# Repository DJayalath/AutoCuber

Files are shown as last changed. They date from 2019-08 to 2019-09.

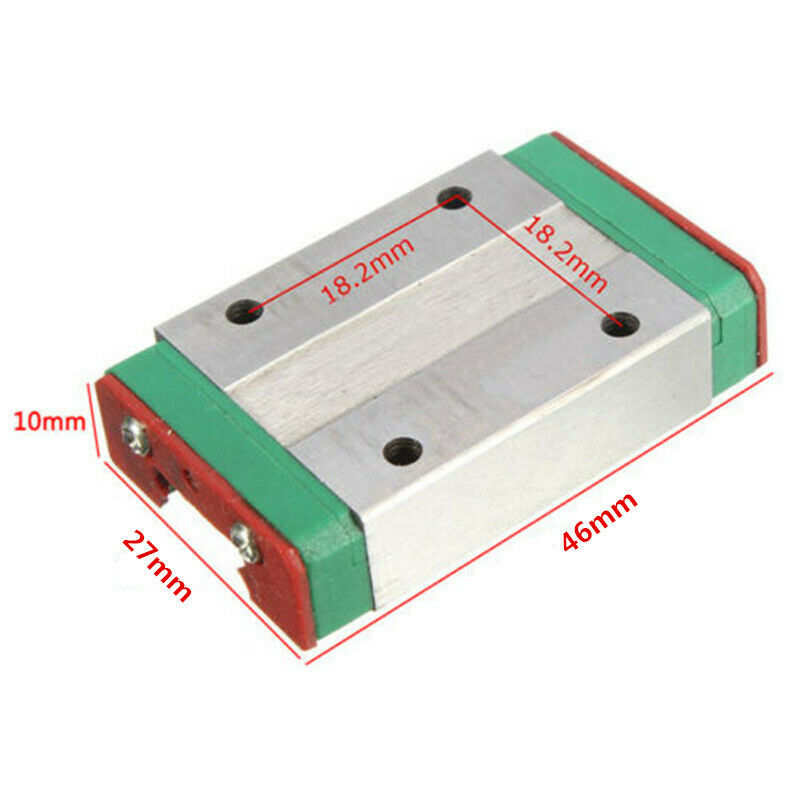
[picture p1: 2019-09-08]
Designs/MGN12H_Block_Measurements.jpg

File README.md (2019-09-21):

# AutoCuber
A fully automated Rubik's cube solving machine

### Video demonstration
Stage 1: Scan all 6 faces of the cube to retrieve cube state

Stage 2: Calculate solution and solve

https://www.youtube.com/watch?v=FX_zLw3P7Gw

(Video recorded prior to optimization updates - current version wastes no rail movements)

### Organisation
- `Designs` contains 3D models created for this project (as well as the custom PCB design)
- `RPI` contains the python programs written to scan in a cube's state and calculate a solution (used on RPI3B w/ Cam)
- The root directory contains the C++ program to control the stepper motors and interpret serial communication (Arduino Mega)

### How does it work?
#### Cube interaction
The machine is similar to others you may have seen before. 4 stepper motors on linear rails are able to turn faces of the cube
in the horizontal plane. 4 more stepper motors attached using a rod can pull and push the other stepper motors along their rails.
Through this system, it is possible to turn any face of the cube, either directly or after rotating the cube. All the motors are 
controlled by DRV8825 stepper motor drivers, connected to an Arduino Mega. The stepper motor drivers are soldered to two identical custom PCBs.
#### Finding the cube's state
A Raspberry Pi 3B is used with a camera to take an image of each face of the cube (Commands are sent to the Arduino Mega to rotate
the cube such that the face needed is facing the camera). The picture is cropped and rotated by a fixed constant amount to contain
only the face of the cube. It is then split into 9 equal segments to isolate individual tiles. k-means clustering is used to find
the dominant colour in each tile. This RGB value is converted to HSL such that linear comparisons can be made between colours. The 
shortest euclidian distance is used to determine which class the colour belongs to. The entire cube is then mapped using this technique.
#### Solving the cube
The `ckociemba` library is used to find a solution using Kociemba's method. The set of instructions to solve the cube are sent 
one by one to the Arduino Mega which uses the motors to complete each move on the cube. **TODO: A custom implementation of 
Kociemba's algorithm.**
### Other Pictures




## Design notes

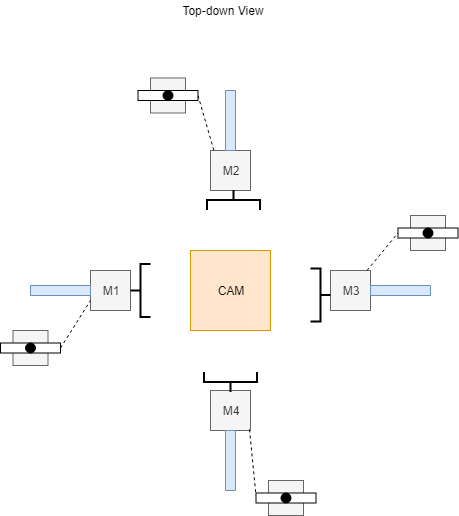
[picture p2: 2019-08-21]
Designs/TopDown.png

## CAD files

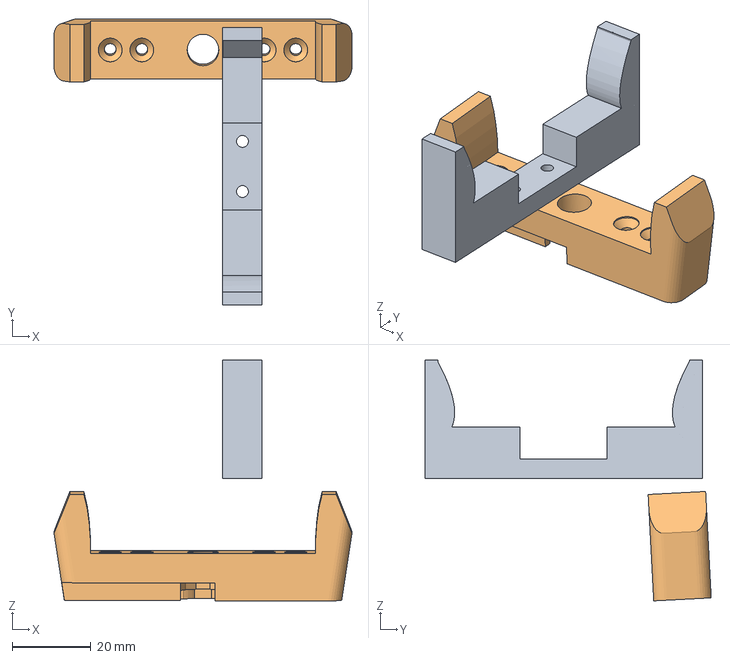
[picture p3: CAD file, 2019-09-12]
Designs/Gripper/Gripper.FCStd
75.5 x 72.6 x 61.0 mm
rcr_gripper

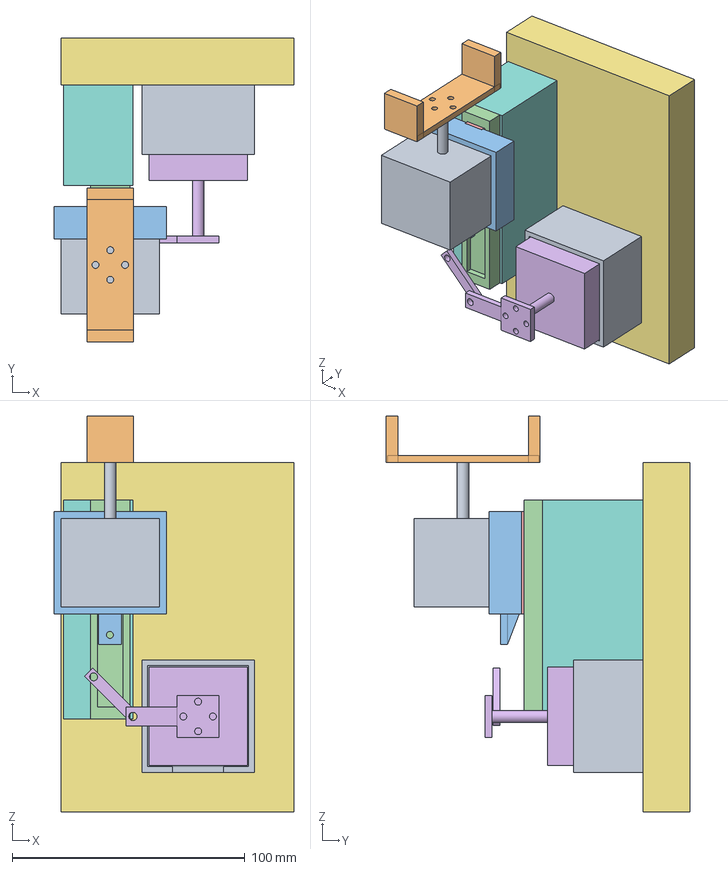
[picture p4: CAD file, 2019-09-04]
Designs/LayoutDesign.FCStd
103.0 x 130.3 x 170.0 mm
17HS4401
Gripper
SildeFullTray
SlidingModule
SlideSection001
SlidingMotorConfig
MechBase
SliderBase
LinearTray

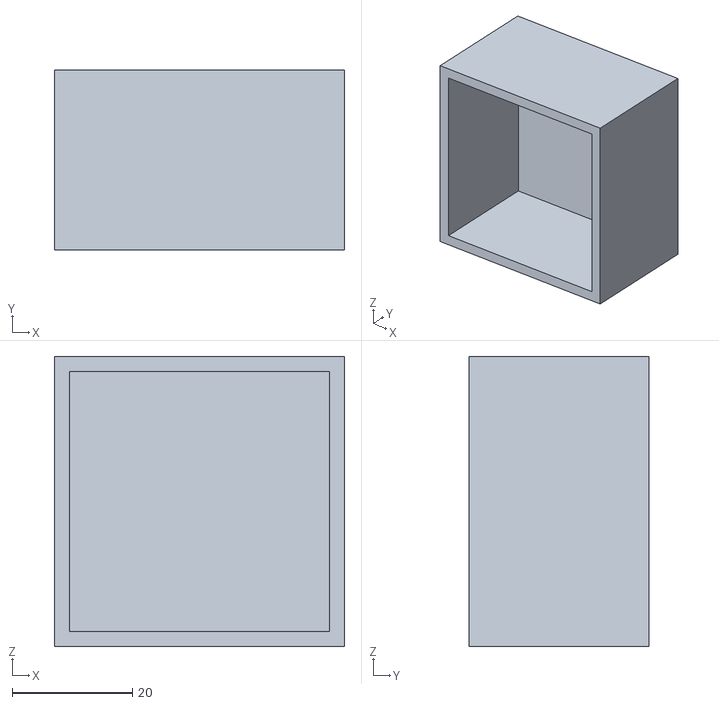
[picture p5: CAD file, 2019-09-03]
Designs/LayoutDesign/LinearMotorTray.stl
48.3 x 30.0 x 48.3

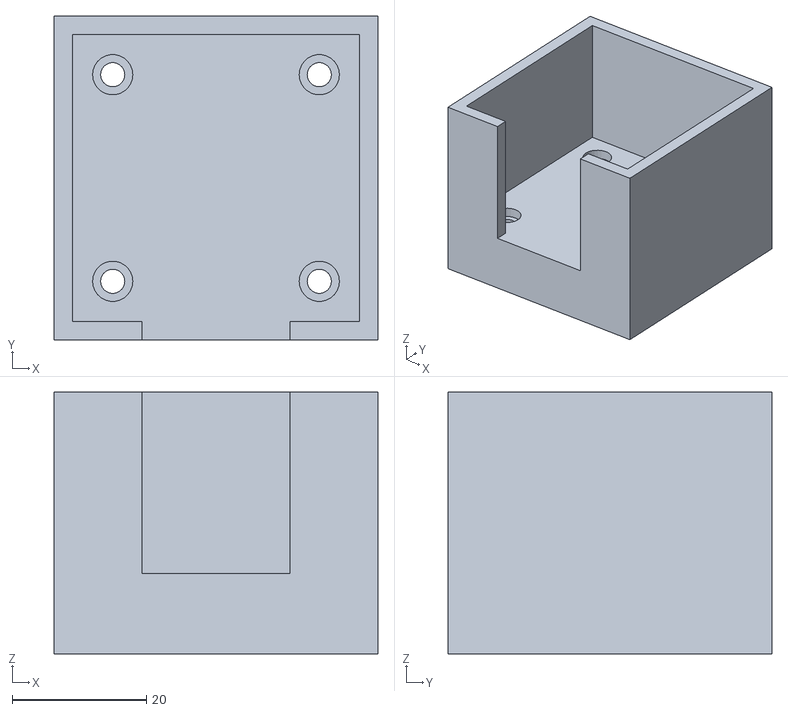
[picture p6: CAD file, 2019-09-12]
Designs/LinearRail/LinearTrayV-1-1.stl
48.3 x 48.3 x 39.0

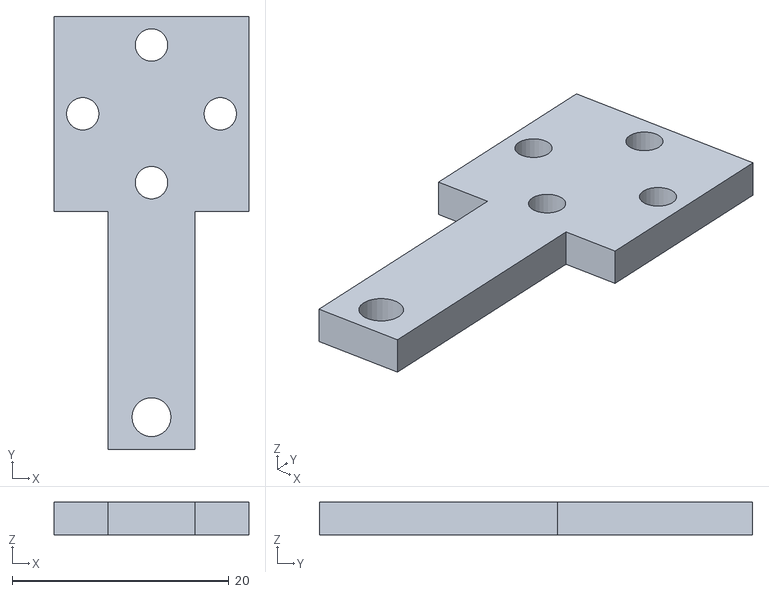
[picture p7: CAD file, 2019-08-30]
Designs/Slider/SlideMotorArmExtension.stl
18.0 x 40.0 x 3.00

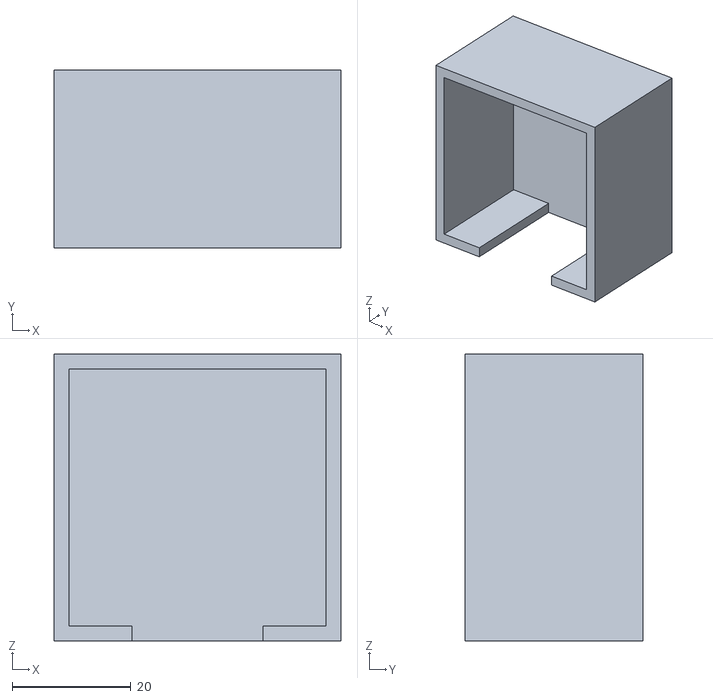
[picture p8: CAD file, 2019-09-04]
Designs/SliderAlt/LinearTray.stl
48.3 x 30.0 x 48.3

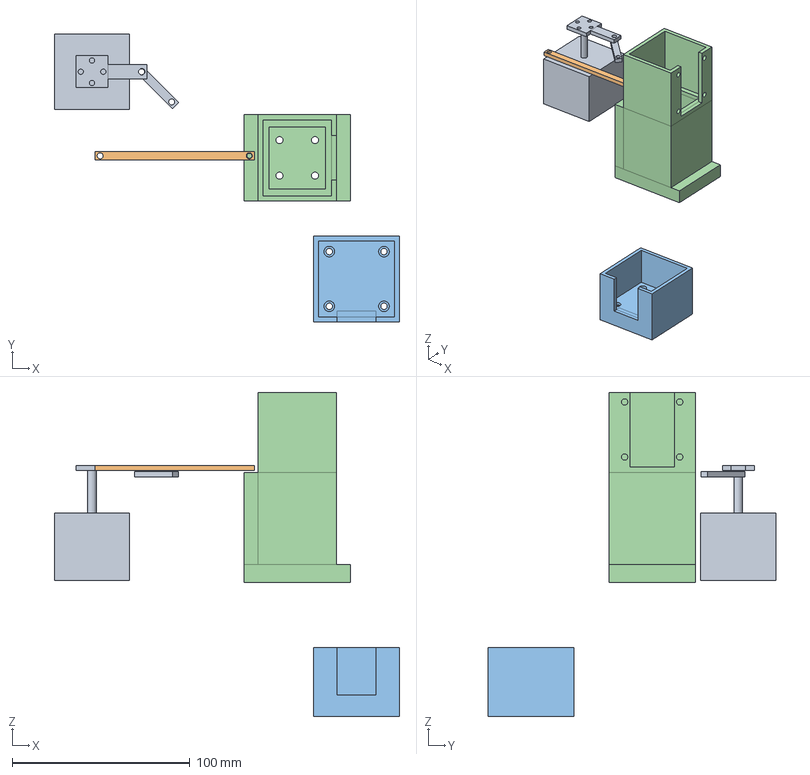
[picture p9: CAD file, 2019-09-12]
Designs/LinearRail/LinearRail.FCStd
194.3 x 162.0 x 182.5 mm
SlidingMotorConfig
SlideArm001

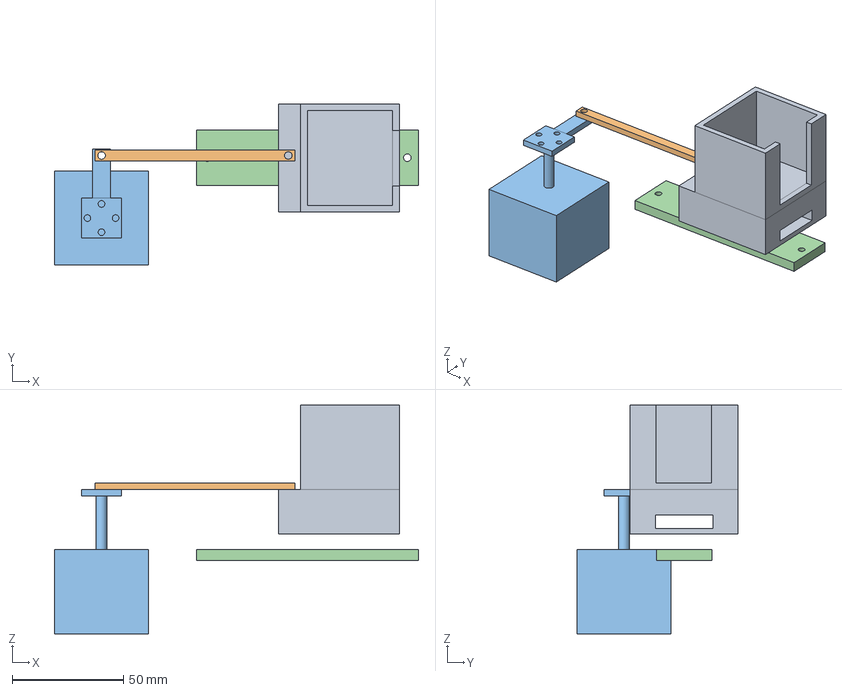
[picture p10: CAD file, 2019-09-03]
Designs/SliderAlt/SliderAlt.FCStd
163.8 x 72.5 x 103.0 mm
SlideArm
SlidingMotorConfig
TraySliderV2

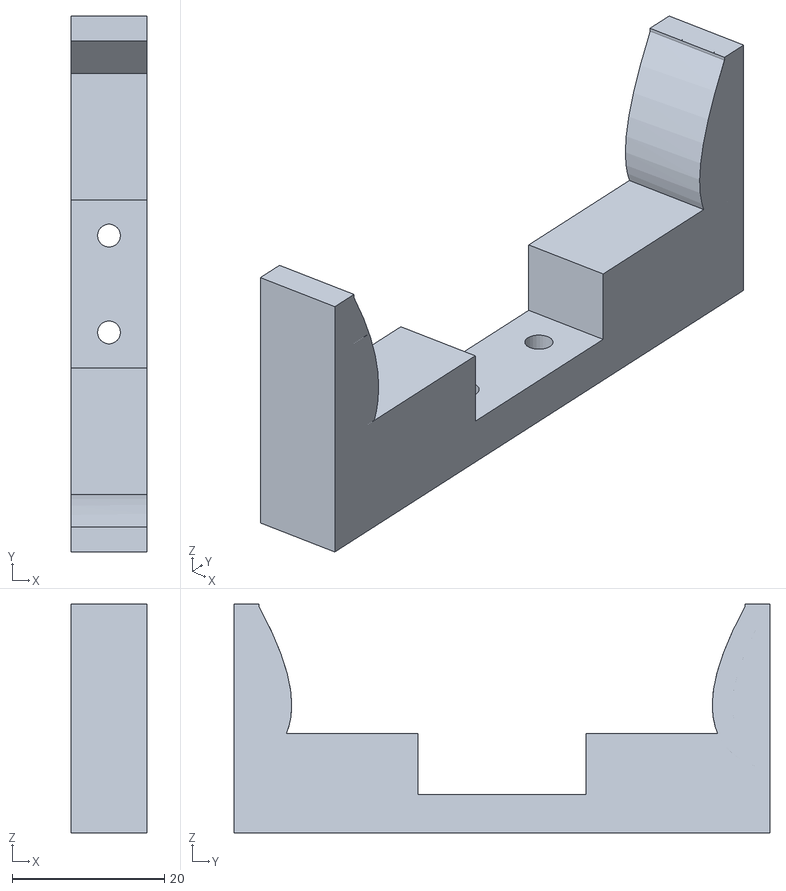
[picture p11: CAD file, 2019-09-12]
Designs/Gripper/Gripper-V-7.stl
10.0 x 70.3 x 30.0

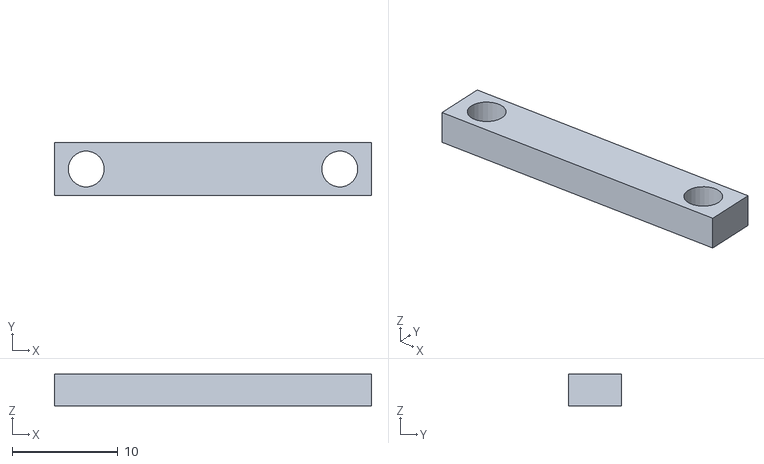
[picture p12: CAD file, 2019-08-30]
Designs/Slider/SlideMotorArm.stl
30.0 x 5.00 x 3.00

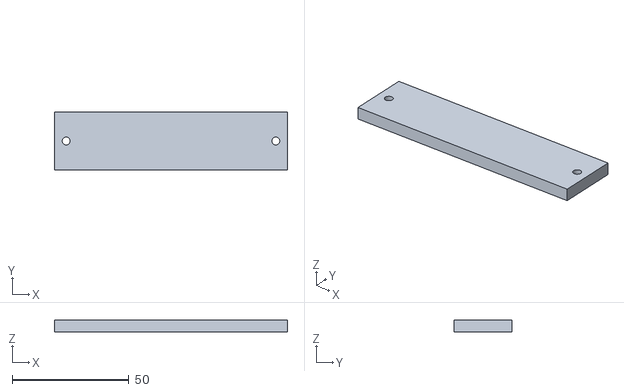
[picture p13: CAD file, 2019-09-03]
Designs/SliderAlt/TraySlider.stl
100.0 x 25.0 x 5.00

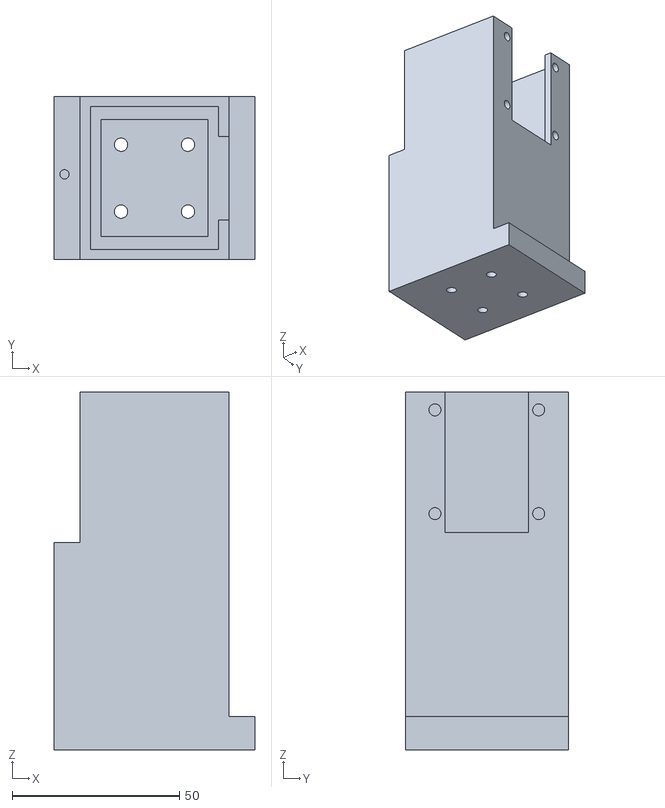
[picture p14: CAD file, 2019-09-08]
Designs/LinearRail/LinearRailV-2.stl
60.0 x 48.8 x 107.0

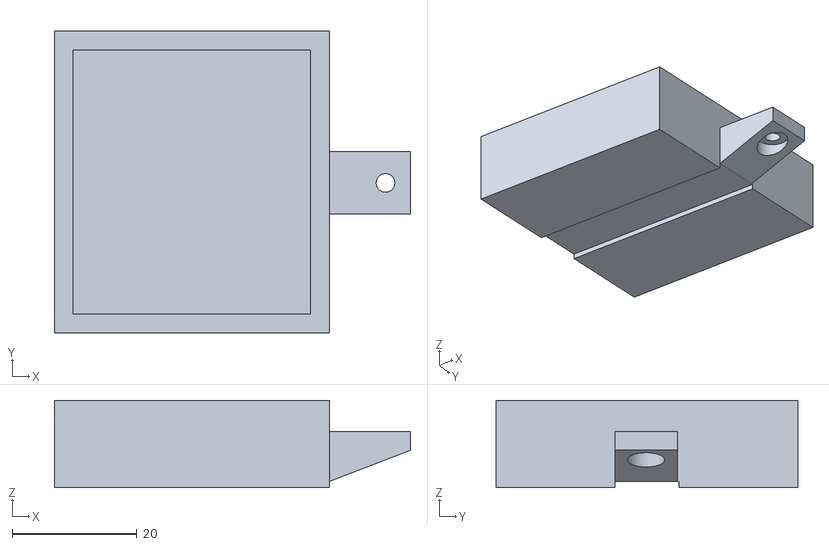
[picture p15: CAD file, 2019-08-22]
Designs/Slider/SliderTray-v0-0-3.stl
57.0 x 48.3 x 14.0

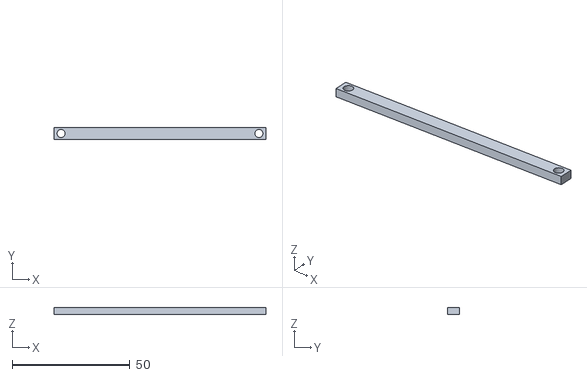
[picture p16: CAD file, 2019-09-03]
Designs/SliderAlt/SlideArm.stl
90.0 x 5.00 x 3.00

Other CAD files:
Designs/Slider/Slider.FCStd
Designs/LinearRail/LinearTrayV-1.stl
Designs/Gripper/Gripper-V-4-2.stl
Designs/Slider/SliderTray-v0-0-2.stl
Designs/Gripper/Gripper Secure.stl
Designs/Gripper/Gripper-V-2-1.stl
Designs/Gripper/Gripper-V-2.stl
Designs/Gripper/Gripper-V-3-1.stl
Designs/Gripper/Gripper-V-3-2.stl
Designs/Gripper/Gripper-V-3-3.stl
Designs/Gripper/Gripper-V-3.stl
Designs/Gripper/Gripper-V-4-1.stl
Designs/Gripper/Gripper-V-4.stl
Designs/Gripper/Gripper-V-5.stl
Designs/Gripper/Gripper-V-6.stl
Designs/Gripper/Gripper.stl
Designs/LinearRail/LinearRailV-1.stl
Designs/Slider/SliderModule.stl
Designs/Slider/SliderSection.stl
Designs/Slider/SliderTray.stl
Designs/SliderAlt/Holder-v-0-1.stl
Designs/SliderAlt/Holder.stl
Designs/SliderAlt/Slider.stl

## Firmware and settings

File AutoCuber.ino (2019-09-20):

// Signal transmission
#include <Wire.h>
// Controlling LCD
#include <LiquidCrystal_I2C.h>
// Resetting arduino
#include <avr/wdt.h>

// Making rotations and moving rails
#include "CubeRotate.h"
// Interpretting rotary encoder inputs
#include "RotaryEncoder.h"

LiquidCrystal_I2C lcd(0x27, 2, 1, 0, 4, 5, 6, 7, 3, POSITIVE);
RotaryEncoder rc(38, 37, 36);
CubeRotate CR = CubeRotate(Rail(2, 3, 4, 5), Rail(6, 7, 8, 9), Rail(22, 23, 24, 25), Rail(26, 27, 28, 29));

// Set starting face
int face = 1;

// Set starting states
bool rpi_ready = false;
bool solve_mode = false;

// Resets arduino after putting rails in default state (extended and vertical)
void reset_device() {
	CR.RestoreDefaultState();
	// Turn on the WatchDog and don't stroke it
	wdt_enable(WDTO_15MS);
	// Do nothing and wait for the eventual...
	for (;;) {}
}

void setup()
{
	// Open serial connection with 9600 bps baudrate
	Serial.begin(9600);

	// Initialise LCD (20 columns, 4 rows)
	lcd.begin(20, 4);
	lcd.clear();
	lcd.backlight();

	// Output starting message
	lcd.setCursor(0, 0);
	lcd.print("AutoCuber");
	lcd.setCursor(0, 1);
	lcd.print("by Dulhan Jayalath");
	lcd.setCursor(0, 2);
	lcd.print("Connecting to RPI3B");
	lcd.setCursor(0, 3);
	lcd.print("Please wait ...");

	MCUSR = 0;  // Clear out any flags of prior resets
}

void loop() {

	// While waiting for connection, send ready signal to RPI
	if (!rpi_ready) {
		delay(200);
		Serial.write(90);
	}

	if (Serial.available() > 0) {

		int rx, iterations;
		// Read one byte in normal mode (Single character instruction)
		if (!solve_mode) {
			rx = Serial.read();
		}
		// Read two bytes in solve mode (Single character instruction + Number of iterations)
		else {
			while (Serial.available() < 2);
			rx = Serial.read();
			iterations = Serial.read() - 48;
		}

		// 79 is RPI ready signal
		if (rx == 79) {

			// Set RPI to ready state
			if (!rpi_ready) {
				rpi_ready = true;
			}

			// Start option selection dialog
			int selection = 0;

			lcd.clear();
			lcd.setCursor(0,0);
			lcd.print("1. Solve Cube");
			lcd.setCursor(0, 1);
			lcd.print("2. Scramble Cube");
			lcd.setCursor(0, 2);
			lcd.print("3. Exit");
			lcd.setCursor(0, 3);
			lcd.print("Selected: 1");
			lcd.setCursor(0, 0);
			lcd.cursor();

			// Change selection on rotation and wait for
			// push button to be pressed
			while (!rc.PollSwitch()) {

				// Get rotation
				int change = rc.PollRotate();

				// Only refresh display if a change is made
				if (change != 0) {
					selection -= change;
					if (selection < 0) {
						selection += 3;
					} else if (selection > 2) {
						selection -= 3;
					}

					lcd.setCursor(10, 3);
					lcd.print(String(selection + 1));
					lcd.setCursor(0, selection);
				}
			}

			lcd.cursor();

			// Act on selection
			switch (selection) {
				case 0:
					lcd.clear();
					lcd.setCursor(0, 1);
					lcd.print("Solving cube...");
					Serial.write(95);
					break;
				case 1:
					lcd.clear();
					lcd.setCursor(0, 1);
					lcd.print("Scrambling cube...");
					solve_mode = true;
					Serial.write(99);
					break;
				case 2:
					Serial.write(98);
					Serial.flush();
					lcd.clear();
					lcd.setCursor(0, 1);
					lcd.print("Powering off...");
					for (;;) {}
					break;
			}
		} else if (rx == 'Z') {
			// Z signal always indicates something has completed and it is
			// now time to reset the arduino
			reset_device();
		}

		switch(rx) {
			// 80 is signal for showing a new face
			case 80:

				// Show the next face
				CR.ShowNext(face);
				// Increment face for next time
				face += 1;

				// Tell RPI that face operation has finished (92 if totally finished, 91 if only side finished)
				if (face > 7) {
					Serial.write(92);
					solve_mode = true;
				} else {
					Serial.write(91);
				}

				break;
			// General rotations
			// 93 message indicates the operation has finished
			case 'R':
				CR.R(iterations);
				Serial.write(93);
				break;
			case 'S':
				CR.R(iterations, true);
				Serial.write(93);
				break;
			case 'L':
				CR.L(iterations);
				Serial.write(93);
				break;
			case 'M':
				CR.L(iterations, true);
				Serial.write(93);
				break;
			case 'U':
				CR.U(iterations);
				Serial.write(93);
				break;
			case 'V':
				CR.U(iterations, true);
				Serial.write(93);
				break;
			case 'D':
				CR.D(iterations);
				Serial.write(93);
				break;
			case 'E':
				CR.D(iterations, true);
				Serial.write(93);
				break;
			case 'F':
				CR.Fr(iterations);
				Serial.write(93);
				break;
			case 'G':
				CR.Fr(iterations, true);
				Serial.write(93);
				break;
			case 'B':
				CR.B(iterations);
				Serial.write(93);
				break;
			case 'C':
				CR.B(iterations, true);
				Serial.write(93);
				break;
			case 'Y':
				CR.Y(iterations);
				Serial.write(93);
				break;
		}

		// Wait for all write operations to complete
		Serial.flush();
	}
}

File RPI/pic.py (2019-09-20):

from picamera import PiCamera
from time import sleep
from PIL import Image
import io
import numpy as np
import scipy
import scipy.misc
import scipy.cluster

# Setup pi camera
camera = PiCamera()
camera.resolution = (1000, 1000)
camera.framerate = 30
sleep(2)
camera.shutter_speed = camera.exposure_speed
camera.exposure_mode = 'off'
g = camera.awb_gains
camera.awb_mode = 'off'
camera.awb_gains = g

def analyse():
    
    stream = io.BytesIO()
    camera.capture(stream, format='png')
    # Rewind stream to start
    stream.seek(0)
    img = Image.open(stream)
    
    #camera.capture('/home/pi/Pictures/image.png')
    #img = Image.open('/home/pi/Pictures/image.png')
    img = img.rotate(46 + 270)
    #img.save('/home/pi/Pictures/image.jpg')
    #img = img.crop((200, 350, 800, 900))
    
    #img = Image.open("/home/pi/Pictures/rubiks-side-B.png")
    #img = img.rotate(2)
    #img = img.crop((110, 95, 475, 460))
    img = img.crop((310, 445, 310 + 365, 445 + 365))
    #img.save('/home/pi/Pictures/cropped.png')
    
    width, _ = img.size
    incr = float(width) / 3.0
    
    colours = []
    for i in range(3):
        for j in range(3):
            # Find dominant colour
            im = img.crop((incr * j, incr * i, incr * j + incr, incr * i + incr)).resize((50, 50))
            #im = cropped_img.resize((150, 150))
            ar = np.asarray(im)
            shape = ar.shape
            ar = ar.reshape(scipy.product(shape[:2]), shape[2]).astype(float)

            # Find clusters
            NUM_CLUSTERS = 6
            codes, dist = scipy.cluster.vq.kmeans(ar, NUM_CLUSTERS)

            vecs, dist = scipy.cluster.vq.vq(ar, codes)
            counts, bins = scipy.histogram(vecs, len(codes))

            index_max = scipy.argmax(counts)
            peak = codes[index_max]
            colours.append([peak[0], peak[1], peak[2]])
    
    # Convert to HSL (H-only) - Ensures lighting independance
    hsl = []
    actual = []
    for colour in colours:
        r = colour[0] / 255.0
        g = colour[1] / 255.0
        b = colour[2] / 255.0        
        mx = max(r, g, b)
        mn = min(r, g, b)
        
        l = (mn + mx) / 2.0
        
        if l < 0.5:
            s = (mx - mn) / (mx + mn)
        else:
            s = (mx - mn) / (2.0 - mx - mn)
        
        if mn == mx:
            s = 0
        
        if mx == r:
            h = (g - b) / (mx - mn)
        elif mx == g:
            h = 2.0 + (b - r) / (mx - mn)
        elif mx == b:
            h = 4.0 + (r - g) / (mx - mn)
        h *= 60
        if h < 0:
            h += 360
        hsl.append((h, s, l))
        if s < 0.45:
            actual.append("w")
        else:
            actual.append("unknown")
    colours = hsl
    
    known_colours = {"r": (342, 0.80, 0.5), "b": (194, 0.98, 0.5), "g": (128, 1.0, 0.5), "y": (78, 1.0, 0.5), "o": (13.7, 0.72, 0.5)}

    for i in range(len(colours)):
        if actual[i] != "w":
            best_dist = 99e9
            best_colour = "unknown"
            for key, value in known_colours.items():
                h, s, l = value
                s *= 360 # Normalize
                a, b, c = colours[i]
                b *= 360 # Normalize
                dist = abs(h - a) + abs(s - b)
                if dist < best_dist:
                    best_dist = dist
                    best_colour = key
            actual[i] = (best_colour)
    
    actual = ''.join(actual)
    #print(colours)
    print("Detected: {0}".format(actual))
#    y = input("Correct? y/n")
#    if y == "n":
#        actual = input("Enter actual: ")
    return actual


def manual_analyse():
    man = input("Enter string: ")
    return man

if __name__ == "__main__":
    analyse()

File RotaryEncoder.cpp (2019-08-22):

#include "RotaryEncoder.h"
#include <Arduino.h>

RotaryEncoder::RotaryEncoder(int encoderCLK, int encoderDT, int encoderSW) : encoderCLK(encoderCLK), encoderDT(encoderDT), pushButton(encoderSW)
{
	pinMode(encoderCLK, INPUT);
	pinMode(encoderDT, INPUT);

	this->previousState = digitalRead(encoderCLK);
}

int RotaryEncoder::PollRotate()
{
	int movement = 0;
	presentState = digitalRead(encoderCLK);
	if (presentState != previousState) {
		if (digitalRead(encoderDT) != presentState) {
			movement++;
		}
		else {
			movement--;
		}
	}
	previousState = presentState;
	return movement;
}

bool RotaryEncoder::PollSwitch()
{
	pushButton.read();
	return pushButton.wasReleased();
}

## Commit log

2019-08-20 Motor spin test code
2019-08-21 Added initial gripper prototype design
    [Gripper.FCStd]
2019-08-21 Re-organised design folder
    Keep model files in separate folders
    [Gripper Secure.stl, Gripper.FCStd, Gripper.stl]
2019-08-22 Created higher level motor driving library
2019-08-22 Using new custom motor driving library
2019-08-22 Designed motor slider for linear mechanism
    [Slider.FCStd, SliderTray.stl]
2019-08-22 Designed custom motor driver PCB
2019-08-22 Rotary encoder reading class
2019-08-22 Using rotary encoder to calibrate stepper motors
2019-08-22 Created a sliding frame model
    [SliderSection.stl]
2019-08-22 Created slider module for tray
    [Slider.FCStd, SliderModule.stl]
2019-08-22 Revised slider tray design
    Tray features a connecting hole for linear movement
    [Slider.FCStd, SliderTray-v0-0-2.stl]
2019-08-22 Refined designs for slider tray
    Improved supports for connector. Added space for nut on 3M screw
    [Slider.FCStd, SliderTray-v0-0-3.stl]
2019-08-30 Created overall layout design model
    [LayoutDesign.FCStd]
2019-08-30 Added connecting designs to slider
    [SlideMotorArm.stl, SlideMotorArmExtension.stl, Slider.FCStd]
2019-08-30 Added mechanism base design
    [LayoutDesign.FCStd]
2019-09-03 Dual motor configuration
2019-09-03 Reworked designs for sliding mechanism
    New designs are much more stable than previous methods
    [Holder-v-0-1.stl, Holder.stl, LinearMotorTray.stl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]
2019-09-04 New designs and code
    [LayoutDesign.FCStd, LinearTray.stl]
2019-09-05 Dual motor driving and simultaneous movement
2019-09-05 2 motor test code
2019-09-05 Redesigned gripper
    Gripper overlaps on sides. Redesign makes gripper thinner and allows 4mm more tolerance
    [Gripper-V-2.stl, Gripper.FCStd]
2019-09-06 5-Motor drive test
2019-09-06 Gripper tolerance reduction
    [Gripper-V-2-1.stl, Gripper.FCStd]
2019-09-06 Gripper arm extension
    Arm length doubled to fix collision with hub mount
    [Gripper-V-3.stl, Gripper.FCStd]
2019-09-06 8-motor test code
2019-09-06 Added stopper to gripper
    Prevents cube movement during rotation
    [Gripper-V-3-1.stl, Gripper-V-3-2.stl, Gripper.FCStd]
2019-09-07 Various gripper revisions
    [Gripper-V-3-3.stl, Gripper-V-4-1.stl, Gripper-V-4-2.stl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]
2019-09-08 New slider design for linear rail
    [Gripper-V-5.stl, Gripper.FCStd, LinearRail.FCStd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]
2019-09-08 Added tray design for rail
    [LinearRail.FCStd]
2019-09-08 Fixed incorrect screw hole distances
    [LinearRail.FCStd, LinearRailV-2.stl, LinearTrayV-1.stl]
2019-09-12 More tray and gripper refinement
    [Gripper-V-6.stl, Gripper-V-7.stl, Gripper.FCStd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]
2019-09-16 Using motor iteration efficiency
